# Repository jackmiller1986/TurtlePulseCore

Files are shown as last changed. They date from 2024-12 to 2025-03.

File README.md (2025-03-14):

# BoxTurtle V1.0
BoxTurtle Automated Filament Control (requires AFC-Klipper-Add-On (Beta))

BT_Render
Join me on Discord (https://discord.gg/eT8zc3bvPR)

BoxTurtle is exactly what it appears to be — an open source AMS style filament changer for [Klipper](https://klipper3d.org) machines. 
BoxTurtle requires the AFC-Klipper Add-On (found [here](https://github.com/ArmoredTurtle/AFC-Klipper-Add-On)).
The goal of BoxTurtle is to deliver a user experience as close to an AMS as possible in vanilla Klipper. i.e. an "AMS" for any klipperized printer regardless of form factor but [VORON Design](https://vorondesign.com) printers in particular.

If you appreciate the work we are doing, you can support us [here](https://www.armoredturtle.com/pages/donate).

# How it works

BoxTurtle is a lane based automated filament changing system. Each lane is equipped with its own dedicated extruder that moves filament to and from the tool head independently. Spool management is done with low drag, top fed electric respoolers.

Each lane merges to a hub (combiner) with a sensor with one outlet that goes to the toolhead.

To accommodate any differences in rotation distance between the extruder in the tool head and the lane motors, BoxTurtle uses a toolhead buffer, like [TurtleNeck](https://github.com/ArmoredTurtle/TurtleNeck) by ArmoredTurtle.

For best results we recommend the AFC-Lite, developed by [Isik's Tech @xbst](https://github.com/xbst/AFC-Lite/) as it has the necessary sensor ports and DC brushed motor drivers used for BoxTurtle's electric respoolers.

# For best results

## AFC Klipper Add-On
BoxTurtle was designed in tandem to work with the [AFC Klipper Add-On](https://github.com/ArmoredTurtle/AFC-Klipper-Add-On). For information on installing and configuring the AFC Klipper Add-On, please visit that repository for the most comprehensive detail. Most common configuration options are prompted for during the installation process.  Some of the options presented are covered below at a high level.

The AFC Klipper Add-On requires root access to your SBC running klipper and the ability to install/modify the installation. Additionally, the minimum version for Klipper/Kalico is 0.12.0 and the minimum version for the klippy-env Python installation is 3.x.

## Filament cutter or tip forming?
BoxTurtle works most reliably with a toolhead filament cutter. Our recommended toolhead cutter solution is [FilamATrix](https://github.com/thunderkeys/FilamATrix). Please visit that Github repository for the most up to date instructions and information. Ensure that toolhead cutting is selected during installing the AFC Klipper Add-On, or enable it manually by editing ``AFC/AFC.cfg`` and restarting Klipper.

If a toolhead filament cutter is not a possibility, tip forming is also an option. This is enabled via the installation script or by editing ``AFC/AFC.cfg`` and restarting Klipper. Tip forming is extremely dependent on your printer, filament and even environment and guidance on properly tuning this is outside the scope of this document. Please visit the [ArmoredTurtle Discord](https://discord.gg/eT8zc3bvPR) for community support on tip forming.

## Filament sensor
A pre-extruder toolhead filament sensor is recommended but not required if using a [TurtleNeck](https://github.com/ArmoredTurtle/TurtleNeck) or [TurtleNeck 2](https://github.com/ArmoredTurtle/TurtleNeck2.0) filament buffer. A post-extruder filament sensor can be defined in the AFC configurations, but is not currently used beyond reporting status of the sensor.

Options include:

- [FilamATrix](https://github.com/thunderkeys/FilamATrix)
- [Filatector](https://github.com/ArmoredTurtle/Filatector)
- [AFC Buffer Ram Sensor using TurtleNeck](https://github.com/ArmoredTurtle/AFC-Klipper-Add-On/blob/main/docs/Buffer_Ram_Sensor.md)

## Waste management

### Pooping, Kicking, and Wiping?
One option for filament purge/waste can be to have the printer 'poop' blobs of filament on the bed, have the nozzle cleaned with a brush/wipe, and hten return the toolhead near the blob and kick off the bed using kinematics into a bucket or other waste evacuation system. This works similar to the method used by [Blobifier](https://github.com/Dendrowen/Blobifier), but does not require servo actuation.  Enabling poop/kick/wipe macros can result in more reliable filament changes and color separation, at the cost of additional time during each filament swap. Each option can be enabled or disabled during the AFC installation process, or by editing ``AFC/AFC.cfg`` and restarting Klipper.

### Prime towers
Filament prime towers can be used standalone, or in combination with the above to minimize the chance that no blobs or oozes from the filament change process make it on to your final print. However, if you are using pooping as described above, you likely need far less purging than the default slicer settings suggest. You can adjust the 'flushing volumes' in most slicers, as well as the size of your prime/purge tower. A decent starting setting for these might be a flushing volume multiplier of 0.1-0.2 and a tower width size of 20mm.

If you want to rely solely on the poop purge, a static size wipe tower can be set by disabling the 'Purge into Prime Tower' setting in your slicer software's "Printer Settings".

Different filament color transitions will require different purge volumes, and thus tuning this is highly dependent on your filaments and prints you are performing.

# Enclosure

The enclosure option for BoxTurtle has been moved to its [own repository](https://github.com/ArmoredTurtle/BoxTurtle-Enclosure). The enclosure is still [under development](https://www.youtube.com/watch?v=Jjgi8q28Y2o), but the most up to date information on it can be found at that repository. Also considering [joining the ArmoredTurtle Discord](https://discord.gg/eT8zc3bvPR) to get progress updates as development progresses.

# Errata
Identified known issues and potential workarounds are documented in [ERRATA.md](ERRATA.md).

# Manual

ArmoredTurtle's project manuals are hosted [here](https://armoredturtle.xyz). There is no PDF, this is intended to make the build experience as easy as possible.
[BoxTurtle Assembly Manual](https://armoredturtle.xyz/manual-sections.html?manual=boxturtle)

# Printed Parts

**IMPORTANT NOTE:** This is NOT a [VORON Design](https://vorondesign.com) project, we strongly recommend that you run a profile that is specific to BoxTurtle. Voron parts profiles are not recommended for BoxTurtle printed parts, as the tolerance expetations are different.

Specifically, make sure you are tuning for skew and filament shrinkage. An excellent tool for this is Vector3D's [Califlower Mk2](https://vector3d.shop/products/califlower-calibration-tool-mk2) (yes, it's worth the $14). Do this *before* you print 1.5-2kg worth of filament for BoxTurtle parts!

If you purchased a kit, all of the parts you need to print are located in the [Base_Build](https://github.com/ArmoredTurtle/BoxTurtle/tree/main/STLs/Base_Build) folder under STLs on this repository. There is also a [web-based configurator](https://armoredturtle.xyz/stl-configurator.html) available for easy identification and download of what STLs to print outside of a base kit build.

All parts are pre-oriented for printing and have all required support pre-built into the STLs. OrcaSlicer/BambuStudio (and possible others) may give warnings about certain parts having 'floating cantilevers', these are breakway support structures and these errors can safely be ignored.

If you have an LDO BoxTurtle kit, these are the options to pick on the web-based configurator:

- ``Would you like normal or monolithic skirts?`` - your choice.  If you can fit monolithic on your printer, it has a more unified look vs the split parts. We recommend a 350mm minimum size bed for this, but you may be able to get them to squeak in on a ~300-305mm plate.
- ``Would you prefer a hub or pass through skirts?`` - Hub is our recommended default choice.
- ``Are you using printed corners or extrusion corners?`` - Printed corners
- ``LED corners or plain?`` - Plain
- ``Are you using D2F or D2HW style switches?`` - D2HW
- ``Would you like to print the Hardware or No-Hardware version of the trays?`` - Choose No Hardware if you have a minimum 235x235mm bed.  Some Ender-style printers have a maximum 220x220mm printable voluem, and so the 'bars' that slot into the extrusion require hardware (heatsets/screws) to attach to the tray.
- ``What style tray would you like to print? Plain, Inlay, Multicolor, or Desiccant?`` - Again, a bit of personal choice.  Plain would be the base option, but there's no reason you couldn't print the others.  An enclosure is [in the works](https://www.youtube.com/watch?v=Jjgi8q28Y2o) so if you wanted to future proof for that, desiccant trays are available (in two sizes).
- ``Would you like to print a TurtleNeck buffer?`` - Yes

If all of the above sounds a bit overwhelming, you can print all of the parts in [LDO_BoxTurtle_Kit_STLs.zip]((https://github.com/ArmoredTurtle/BoxTurtle/tree/main/STLs/STLs/LDO_BoxTurtle_Kit_STLs.zip) and they will be the right ones to build a functioning BoxTurtle.

For the 'No Hardware' trays, you may wish to enable 'Thick bridges' or use a 0.25mm first layer height, as otherwise the built in supports may generate 0.4mm gap between the support and the printed part.  The N20 motor mounts may also benefit from an 0.25mm first layer height.

There is a calibration print that you may like to print before getting started [here](https://www.printables.com/model/1004303-box-turtle-calibration-fidget).

# How to create a meshed look on the skirts
There are a few ways to create a 'meshed' look on the hexes on the skirts, using your slicer.

- On the print settings profile, set top and bottom layers to 0.  Adjust infill pattern, density and angle to suit your preference.
- You can also do a height range modifier on the part from 0-3.6mm to set top/bottom layers to 0, and infill pattern, desnity and angle to suit your preference.
- If you would like a different color for the hexes, you can do a color swap at layer 19 (3.8mm with 0.2mm layer heights).
- [SteveBuilds](https://youtube.com/@SteveBuilds) created a custom set of skirt options with modeled in hexes and multibody parts, these can be found [here (multibody)](https://github.com/ArmoredTurtle/BoxTurtle/tree/main/STLs/Option_Parts/Skirts/Multibody/) and [here (modeled hex meshes)]((https://github.com/ArmoredTurtle/BoxTurtle/tree/main/STLs/Option_Parts/Skirts/Hex_Mesh/). To get a two tone color look, perform a color change at 3.2mm (layer 16 at 0.2mm print heights).

# Wiring
BoxTurtle_AFC-Lite_Pinout

Refer to [BT_Wiring/README.md](BT_Wiring/README.md) for recommended wire lengths for each lane.

# PTFE sizes/lengths

**NOTE**: PTFE lengths between extruder to hub are suggested starting lengths - you may need to trim a little bit off in order for it to have a smooth bend. The filament path should be a smooth curve without tight corners.

| Component | Outer Diameter | Inner Diameter | Length | Notes |
|---|---|---|---|---|
| Feeders to Trigger | 4mm | 3mm | 50mm | Quantity 4 ; use PTFE cutter jig |
| Trigger to Extruder | 4mm | 3mm | 80mm | Quantity 4 ; use PTFE cutter jig |
| Extruder to Hub (Outer lanes) | 4mm | 2mm | 171mm | Quantity 2; 3mm ID will blow out. A chamfer is recommended on each end. |
| Extruder to Hub (Inner lanes) | 4mm | 2mm | 101mm | Quantity 2; 3mm ID will blow out. A chamfer is recommended on each end. |
| Hub to Turtleneck | 4mm | 2mm | build dependent | A chamfer is recommended on each end. |
| Turtleneck to toolhead | 4mm | 2-3mm | build dependent | Existing bowden tube is fine, but tighter ID can also be used. |

# Initial startup guide
Please refer to the [Initial Startup Guide](Initial_Startup.md) after completing the assembly of your BoxTurtle for next steps.

# Optional Accesories
Some optional printed accesories for your BoxTurtle build can be found on the [AFC-Accessories](https://github.com/ArmoredTurtle/AFC-Accessories) repository.

# BoxTurtle sourcing/vendors
While BoxTurtle can be mostly self-sourced, some vendors offer partial or full BoxTurtle kits. These vendors also have dedicated channels on the Armored Turtle Discord.

If you purchase a kit from a vendor not on this list, it has not been validated in any way by the ArmoredTurtle team for either quality or completeness. For best results we recommend using a trusted vendor from the list below whenever possible. If you are a vendor and would like to be added to this list, please open a ticket on our Discord to request being added.

US:
- [DLLPDF](https://dllpdf.com) sells a [BoxTurtle frame kit](http://dllpdf.com/box-turtle-frame)
- [Isik's Tech](https://store.isiks.tech/) has BOM parts, including full kits [here](https://store.isiks.tech/collections/box-turtle-parts). Isik's Tech also ships internationally.
- [Fabreeko](https://www.fabreeko.com/products/box-turtle?_pos=4&_psq=box&_ss=e&_v=1.0)
- [KB3D](https://kb-3d.com/store/boxturtle/2132-pre-order-ldo-box-turtle-automated-filament-changer-kit-v10.html)
- [West3D](https://west3d.com/products/box-turtle-automated-filament-changer-multi-material-unit-by-armored-turtle)
  
CA:
- [Sparta3D](https://sparta3d.ca/products/ldo-box-turtle-kit)

EU:
- [Alchemy3D.de](https://alchemy3d.de) has a [BOM in a box kit](https://alchemy3d.de/products/boxturtle)
- [Lab4450.com](https://lab4450.com) resells the [AFC-Lite MCU](https://lab4450.com/product/afc-lite-board/)
- [3DO](https://3do.dk/3d-printer/2946-ldo-boxturtle-afc-kit-til-klipper-printere-forudbestilling.html)

UK:
- [OneTwo3D.co.uk](https://www.onetwo3d.co.uk)
- [Desktop Machine Shop](https://www.desktopmachineshop.com/shop/ldo-boxturtle-afc-kit-v1-0-163?category=4#attribute_values=)
- [Viperworx](https://www.viperworx.uk/product/box-turtle-enclosure-panels-by-armored-turtle)
  
AU:
- [DREMC](https://store.dremc.com.au/products/ldo-box-turtle-hardware-kit)
  
# Merch
- BoxTurtle T-Shirt ($3 from each sale goes to support ArmoredTurtle) via [Cotton Bureau](https://cottonbureau.com/p/QKF5XC/shirt/colored-box-turtle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)- also has sweatshirt/hoodie variants
- BoxTurtle Sticker via [Dr. Mursey](https://drmursey.myshopify.com/products/box-turtle)

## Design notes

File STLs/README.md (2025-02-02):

We have an automatic STL configurator wizard if you need help figuring out what parts to print!

https://armoredturtle.xyz/stl-configurator.html

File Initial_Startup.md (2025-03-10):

# BoxTurtle Initial Startup/Commissioning guide

The following guide will help you on the journey to multicolor printing after you have physically completed the [assembly of your BoxTurtle](https://armoredturtle.xyz).

## Prerequisites

### Calibrate/tune existing printer extruder
If you are installing this on a new printer or extruder (including [FilamATrix](https://github.com/thunderkeys/FilamATrix) ensure you have calibrated your printer/extruder before introducing AFC/multicolor printing. If your extruder rotation distance is off by a large factor, this will cause issues with defining values such as ``tool_stn`` and others later on in the configuration.

It is a lot easier to do some of the calibrations (such as rotation distance) *BEFORE* installing your BoxTurtle.

Our recommended guide to follow for calibration is [Ellis' Print Tuning Guide](https://ellis3dp.com/Print-Tuning-Guide/).

### Ensure minimum system requirements
The AFC Klipper Add-On requires a minimum Klipper/Kalico version of 0.12.0, as well as a correspoding klippy-env python environment at least 3.x.

If you are on Klipper/Kalico 12, but running ``~/klippy-env/bin/python --version`` returns version 2.7.x, you can recreate it with the following.

```
sudo service klipper stop

mv ~/klippy-env ~/klippy-env2.7
virtualenv -p python3 ~/klippy-env
~/klippy-env/bin/pip install -r ~/klipper/scripts/klippy-requirements.txt

sudo service klipper start
```

After recreating it, you may need to reinstall any custom add-ons, such as Klippain Shake&Tune, TMC Autotune, etc.

Ensure you have a clean, functioning klipper install with all of these minimum requirements met before proceeding to the next step.

## Flashing the AFC-Lite board

The AFC-Lite MCU can be connected with either CANBUS or USB.

If you choose to use CANBUS, follow [this guide from Esoterical](https://canbus.esoterical.online/toolhead_flashing/common_hardware/AFC-Lite/README.html).  This site also has a wealth of information on how to configure CANBUS if this is your first time using it.

If you choose to use USB, you will still need to run a 24 V+/V- cable to the AFC-Lite canbus port, just leave the CAN High/Low pins unpopulated. To flash the AFC-Lite for use with USB for data, follow [this guide from Esoterial](https://usb.esoterical.online/hardware_config/STM32/AFC_Lite.html)

Further details regarding the AFC-Lite can be found [in the AFC-Lite manual](https://github.com/xbst/AFC-Lite/blob/master/Docs/AFC-Lite_Manual.pdf).

After flashing and setting up connections/configurations appropriately, you should be able to either obtain the CANBUS UUID (if using CAN) or the device serial path (e.g., ``/dev/serial/by-id/...``) (if using USB) for the AFC-Lite MCU.  Please ensure you have these values before you proceed, as they will be required.

## Make note of any toolhead sensor pins
If you are using [FilamATrix](https://github.com/thunderkeys/FilamATrix), and are using toolhead endstop sensors, make a note of what MCU pins those sensors are connected for the pre-extruder gear sensor (aka ``pin_tool_start``) and post-extruder gear sensor (``pin_tool_end``). Use these in the next step to properly install and configure AFC.

If you do not have a native toolhead filament sensor, you can use either an inline filament sensor such as [Filatector](https://github.com/ArmoredTurtle/Filatector), or you can use the [TurtleNeck buffer](https://github.com/ArmoredTurtle/TurtleNeck) as a virtual toolhead endstop, please see [this guide](https://github.com/ArmoredTurtle/AFC-Klipper-Add-On/blob/main/docs/Buffer_Ram_Sensor.md) for more details.

## Install the AFC Klipper Add-On
BoxTurtle works best with the [AFC Klipper Add-On](https://github.com/ArmoredTurtle/AFC-Klipper-Add-On).  The rest of this guide will focus on configuring AFC for use with BoxTurtle.

Follow the instructions on that Github for latest details on installation and configuration, but at the time of writing this is the easy button:

```
cd ~
git clone https://github.com/ArmoredTurtle/AFC-Klipper-Add-On.git
cd AFC-Klipper-Add-On
./install-afc.sh
```

The default options for the park, cut, kick, wipe, and tip forming macros can be used if you don't know what to choose. These can all be changed later by editing ``AFC/AFC.cfg`` and doing a firmware restart.

After installation, please ensure sure you update the following settings:
- In ``AFC/AFC_Turtle_1.cfg``:
  - ``canbus_uuid`` if using CANBUS
  - ``serial`` if using USB
- In ``AFC/AFC_Hardware.cfg``
  - ``pin_tool_start`` and/or ``pin_tool_end``

In your ``printer.cfg``'s ``[extruder]`` section, update the setting ``max_extrude_only_distance`` to the value 400.  If the setting is not there, add it:

```max_extrude_only_distance: 400```

For best results, reboot your printer after installing the Add-On and including it in your printer.cfg.  This will ensure all required modules are enabled.

## First self-test
AFC will run a self-test automatically on startup. It will run through the respoolers on each lane (from left to right, lanes 1-4) and will update the lightbox LED indicating status for each lane.

The default status indicators are:

- Red: No filament loaded/detected at extruder sensor
- Green: Filament loaded to lane extruder sensor
- Blue: Filament loaded to toolhead
- White: Filament in process of being loaded

After the self-test completes, you hopefully will see a picture of a happy turtle in the console log! If you get a picture of an error turtle, you may have a misconfigured AFC setting, broken pin or some other issue that needs attention.

You can display the status of sensors in Mainsail/Fluidd as regular filament switches by setting ``enable_sensors_in_gui: True`` either globally in ``AFC/AFC.cfg`` or in the individual component section (e.g. extruders in ``AFC/Turtle_1.cfg``.

If you are unable to resolve the error after visiting the [troubleshooting guide](https://github.com/thunderkeys/AFC-Klipper-Add-On/tree/main?tab=readme-ov-file#troubleshooting), you can get support from the community on the Armored Turtle discord by opening a help thread (run the Discord command ``/help``) to learn how).

## Further tests

### Respoolers
Run the ``TEST`` command against each lane (one at a time) to verify proper respooler operation:
- ``TEST LANE=lane1``
- ``TEST LANE=lane2``
- ``TEST LANE=lane3``
- ``TEST LANE=lane4``

Verify that each respooler works properly before proceeding.

### Trigger switches
Actuating the trigger switch should begin pulsing that lane's extruder motor to load filament.  Verify that the switch being actuated is activating that same lane's extruder motor.

Once all four lanes are confirmed to be activating the correct extruder when the trigger switch is actuated, move on to the next step.

### Extruders
Insert filament into the feeder tube (it helps to cut it at an angle) and press through until the extruder motor gears catch the filament and load it further.  If you can press the filament through but it feels like the extruder motor is pushing back on the filament instead of pulling it in, try reversing the ``dir_pin`` setting for that extruder motor in ``AFC/AFC_Turtle_1.cfg``.

If you are able to load filament into all 4 lanes and get a green LED indicator, and ``AFC_STATUS`` at the console reports no errors, move on to the next step.

### TurtleNeck buffer
Test that TurtleNeck buffer is configured correctly by extending the slide all the way out, then run ``QUERY_BUFFER BUFFER=Turtle_1``.  This should return ``Trailing``.  Collapse the slide all the way so it triggers the switch at the rear, then rerun the QUERY_BUFFER command.  It should then report ``Advancing``.

Confirm proper operation of your TurtleNeck before proceeding.

## Setting up hotend specific values
Some of the values with AFC are extremely dependent on your hotend.

Suggested starting values for hotend types (more to be added later).  ``tool_stn`` and ``tool_stn_unload`` are in ``AFC/AFC_Hardware.cfg``, ``variable_retract_length`` and ``variable_pushback_length`` are in ``AFC/AFC_Macro_Vars.cfg``.  For ``tool_stn``, if you have ``pin_tool_end`` defined, use the second value; otherwise, use the first value. You may need to increase this value if you are using a ram buffer as the toolhead sensor.

| Hotend | tool_stn | tool_stn_unload | variable_retract_length | variable_pushback_length
| ------ | -------- | --------------- | ----------------------- | ------------------------
| Revo Voron | 52 (if ``pin_tool_end`` is NOT defined) / 29 (if ``pin_tool_end`` is defined) | 62 | 22 | 20 |
| Rapido HF | 64.1 (if ``pin_tool_end`` is NOT defined) / 41.1 (if ``pin_tool_end`` is defined) | 105.9 | 10 | 10 |
| Rapido V2 HF | 74 (if ``pin_tool_end`` is NOT defined) / 52 (if ``pin_tool_end`` is defined) | 81 | 25 | 20 |

## Setting up macro variables

### A note on order of operations of macros during tool changes
AFC will perform macros (if enabled) on each tool change (``T0``, ``T1``, etc) in the following order:

- Load sequence
  - If toolhead is loaded from another lane, that will first be unloaded (see below sequence)   
  - Poop
  - Wipe/Brush
  - Kick
  - Wipe/Brush
  - Print 
- Unload sequence
  - If toolhead cutter is enabled:
     - Cut
     - Park
  - If tip forming is enabled:
     - Park
     - Tip Form

### Uncommon variables
AFC has many variables that you can tweak for macros, including definition of complete custom macros to replace the stock ones. Most users will never need to touch these and they will not be covered in this guide. Below are the most common variables that will need adjusting for a stock BoxTurtle configuration with a Stealthburner/FilamATrix toolhead.

For more details, please refer to the AFC-Klipper-Add-On Github docs or the comments in the ``AFC/AFC.cfg`` and ``AFC/AFC_Macro_Vars.cfg`` files.

If you chosen not to enable a macro during the installation, the command will still show in mainsail, and have a configuration in AFC_Macro_Vars.cfg, but it will not be called during the load/unload sequences.

#### Park
The park macro is enabled or disabled by setting the ``park`` variable in ``AFC/AFC.cfg`` (this is prompted for during the install script, but you can change it at any time and do a firmware restart to enact the change.)

Adjust the following macro variables in ``AFC/AFC_Macro_Vars.cfg`` for the park macro (if enabled) for your specific printer.
  - ``variable_park_loc_xy`` - This is the X,Y coordinate your toolhead will park at prior to other filament changes.

#### Cut
The cut macro is enabled or disabled by setting the ``tool_cut`` variable in ``AFC/AFC.cfg`` (this is prompted for during the install script, but you can change it at any time and do a firmware restart to enact the change.)
Adjust the following macro variables in ``AFC/AFC_Macro_Vars.cfg`` for the cut macro (if enabled) for your specific printer. 
  - ``variable_retract_length`` - How much to retract filament before performing the cut. This reduces purge waste and improves reliability of insertion of the next filament. Hotend dependent, a good starting value is the length of your meltzone. Please see the hotend diagrams for suggested values. The default is ``20``.
  - ``variable_pin_loc_xy`` - X,Y position where your toolhead cutter arm *just* touches the depressor pin.  There is no default value, this must be defined.
  - ``variable_cut_direction`` - For FilamATrix, you want this to be set to ``left``. Other toolhead cutters may actuate in a different direction (e.g., Dragon Burner cutter may be ``front``).  The default value is ``left``.
  - ``variable_pin_park_dist`` - How far to park the toolhead near the depressor pin before initiating the move. This acts as a safety as well as helps generate momentum for the cut. The default value is ``6.0``.
  - ``variable_cut_move_dist`` - How far the toolhead has to move from ``variable_pin_loc_xy`` to fully depress the cutter. This should be reduced from the actual value by 0.5mm as a buffer to prevent skipped steps. The default value is ``8.5``
  - ``variable_cut_count`` - How many times to attempt the cut. The default value is ``2``, to ensure a clean/complete cut.

#### Poop
The poop macro is enabled or disabled by setting the ``poop`` variable in ``AFC/AFC.cfg`` (this is prompted for during the install script, but you can change it at any time and do a firmware restart to enact the change.)

Adjust the following macro variables in ``AFC/AFC_Macro_Vars.cfg`` for the poop macro (if enabled) for your specific printer.
  - ``variable_purge_loc_xy`` - X,Y position where to perform the poop operation. Usuually, this is on the corner of your bed.

#### Kick
The kick macro is enabled or disabled by setting the ``kick`` variable in ``AFC/AFC.cfg`` (this is prompted for during the install script, but you can change it at any time and do a firmware restart to enact the change.)
Adjust the following macro variables in ``AFC/AFC_Macro_Vars.cfg`` for the kick macro (if enabled) for your specific printer.
  - ``variable_kick_start_loc`` - the X, Y, Z location to move to prior to begin the kick operation. If you do not want a Z move, set the Z coordinate to ``-1``.
  - ``variable_kick_direction`` - the direction to move to kick the poop off (left, right, front, back)
  - ``variable_kick_move_dist`` - how for to move in that direction to kick the poop off

#### Wipe/Brush
The wipe macro is enabled or disabled by setting the ``wipe`` variable in ``AFC/AFC.cfg`` (this is prompted for during the install script, but you can change it at any time and do a firmware restart to enact the change.)
Adjust the following macro variables in ``AFC/AFC_Macro_Vars.cfg`` for the brush macro (if enabled) for your specific printer.
  - ``variable_brush_loc`` - X, Y, Z coordinates of the center of the brush. If you do not want a Z move, set the Z coordinate to to ``-1``.
  - ``variable_y_brush`` - Set to ``true`` if you want the macro to do a brush in the Y direction first before doing X. When set to ``false``, only it will move only in the X direction.
  - ``variable_brush_width`` and ``variable_brush_depth`` - the width and depth of your brush, in mm.
  - ``variable_brush_count`` - Number of passes to make on the brush, the default is ``4``.

#### Tip forming
**NOTE**: While a toolhead cutter is recommended for best results, if you do not have one you will need to configure tip forming. The full process for this is outside the scope of this document and will be very hotend and perhaps even filament dependent. If using a 'Hub Cutter' (e.g., BT-Snappy or EREC) you will still likely need to do tip forming to prevent stringy tips from getting jammed in the toolhead, hub or BoxTurtle extruder gears.

Tip forming is enabled or disabled by setting the ``form_tip`` variable in ``AFC/AFC.cfg`` (this is prompted for during the install script, but you can change it at any time and do a firmware restart to enact the change.)

Adjust the following tip forming variables in ``AFC/AFC.cfg`` for tip forming (if enabled) for your specific printer. Note the different location that the above macros.
  - ``cooling_tube_position`` - Starting location of the cooling tube in mm (based off toolhead sensor)
  - ``cooling_tube_length`` - Length of the cooling move in mm
  - ``cooling_moves`` - number of cooling moves to perform, the default is ``4``.

### Enacting changes
Perform a ``FIRMWARE_RESTART`` (a full printer reboot is not required) after adjusting all the macro variables in ``AFC/AFC_Macro_Vars.cfg`` file.

## Calibration
Follow [this guide](https://github.com/thunderkeys/AFC-Klipper-Add-On/blob/main/docs/Calibration.md) to calibrate the necessary lengths of your BoxTurtle.

Note that these values may need to be tweaked slightly if the loading sequence does not function.  Make small adjustments (5/10mm) to see if performance/reliability improves.

## First load of filament to toolhead

You're now ready to attempt your first Automated Filament Control action!

- Home your printer (using G28 or Mainsail/Fluidd GUI buttons)
- Heat the hotend to your filament's extrusion temperature (e.g., PLA 210, ABS 260, etc).
- Load the filament for lane 1 with with the ``T0`` command.
- Confirm that filament travels to the toolhead and performs any configured poop or wipe actions.  After the load has successfully completed, test that you are able to manually extrude filament using the console/GUI.
- Change filament to lane 2 using the ``T1`` command.  Confirm that the toolhead moves to the park position, performs the cut (or tip shaping, if not using a cutter), retracts the filament for lane 1 back to the BoxTurtle hub.  It will then load the filament in lane 2 to the toolhead, and perform the poop, wipe, kick and wipe macros.
- Repeat this process for lane 3 (``T2``) and lane 4 (``T3``).

If you are able to successfully load and unload filament without intervention, you are ready to move on to the next step. Almost there!

### Configuring your slicer

The recommended slicer for AFC is OrcaSlicer. Other slicers such as PrusaSlicer or SuperSlicer may be used, and the configuration of options within them is similar but naming or options may be slightly different.

#### Updating printer settings in Orca
For the printer you are adding BoxTurtle to, first go to the Printer settings, Multimaterial tab and ensure settings are configured as per the below screenshot.
![Orca_Printer_Settings](https://github.com/user-attachments/assets/1aa56051-dbbf-49a4-b818-368e00406b17)

Also, on the Extruder 1 setting page - reduce ``Retraction while switching material`` length from the default of 2 to 0.5. (PrusaSlicer/SuperSlicer users, this default is 10mm and is on each extruder under the printer settings).

#### Adding additional filaments/extruders
Increase the number of filaments to match your BoxTurtle's lane count. 
![Orca_Add_Filament_Settings](https://github.com/user-attachments/assets/61fb26a4-57c6-4624-8435-478d719a01ae)

#### Updating the Machine G-code settings

- Set ``Machine start G-code` appropriately for your printer, specifically adding the ``TOOL={initial_tool}`` to your ``PRINT_START`` macro.
```
M104 S0 ; Stops OrcaSlicer from sending temperature waits separately
M140 S0 ; Stops OrcaSlicer from sending temperature waits separately
PRINT_START EXTRUDER=[nozzle_temperature_initial_layer] BED=[bed_temperature_initial_layer_single] TOOL={initial_tool}
```

- Set ``Change Filament G-Code`` to the below value.  Remove any other custom code here, e.g. extruder moves.
```
T[next_extruder]
```

#### Additional Slicer configuration - pre-OrcaSlicer 2.2.0
Configuring per-material filament ramming is no longer required as of the official OrcaSlicer 2.2.0 release (PR [#6934](https://github.com/SoftFever/OrcaSlicer/pull/6934)).  If you are on an earlier version than that (including betas/release candidates) you will need to make the following additional changes to your slicer configurations.
#### Material Settings
![Orca_Material_Settings](https://github.com/user-attachments/assets/a1569e5a-24c5-48f9-98fb-26465bf7c75c)
##### Ramming Settings
Because the AFC-Klipper-Add-On handles any tip forming in the extension, we need to disable these specific settings in the slicer software.  Below is a screenshot for OrcaSlicer, but most Slic3r-based slicers have a similar dialog/setting.
![Orca_Ramming_Settings](https://github.com/user-attachments/assets/2744fb86-afae-4645-9215-3f8507558509)

## Updating your PRINT_START macro
#### *Please note this is just an example macro to show how to incorporate the initial tool into your print start macro. Please adjust it to match your printer setup. A good starting point for a PRINT_START macro is [jontek2's "A Better PRINT_START macro"](https://github.com/jontek2/A-better-print_start-macro)*

Add the TOOL parameter we added to the Machine start G-Code earlier to your PRINT_START macro.

```
[gcode_macro PRINT_START]
gcode:
  {% set BED_TEMP = params.BED|default(60)|float %}
  {% set EXTRUDER_TEMP = params.EXTRUDER|default(195)|float %}
  {% set S_EXTRUDER_TEMP = 150|float %}
  {% set initial_tool = params.TOOL|default("0")|int %}

  G90 ; use absolute coordinates
  M83 ; extruder relative mode

  G28 # Home Printer
  # Do any other leveling such as QGL here

  AFC_PARK

  M140 S{BED_TEMP} # Set bed temp
  M109 S{EXTRUDER_TEMP} # wait for extruder temp
  T{initial_tool} #Load Initial Tool

  M104 S{S_EXTRUDER_TEMP} # set standby extruder temp
  M190 S{BED_TEMP} # wait for bed temp

  G28 Z

  # Bedmesh or load bedmesh

  AFC_PARK
  M109 S{EXTRUDER_TEMP} ; wait for extruder temp

  # Add any pre print prime/purge line here
  # Start Print
```

If you are modifying an existing macro:
- Add the following to the top of the PRINT_START macro just under the ``gcode:`` line
```
  {% set BED_TEMP = params.BED|default(60)|float %}
  {% set EXTRUDER_TEMP = params.EXTRUDER|default(195)|float %}
  {% set S_EXTRUDER_TEMP = 150|float %}
  {% set initial_tool = params.TOOL|default("0")|int %}
```
- Home the printer using ``G28``
- Set hotend to extrusion temperature ``M104 S{EXTRUDER_TEMP}``
- Load the first filament to be used with ``T{initial_tool}``
- Move to park position with ``AFC_PARK``
- Lower the hotend to standby temperature with ``M104 S{S_EXTRUDER_TEMP}``
- Perform any other necessary pre-flight tasks (e.g., heat soak, re-homing Z, bed meshing, prime/purge line, etc)

## Troubleshooting
If you get a klipper error about GSTAT Resets as in the example below:

```
TMC 'AFC_stepper lane1' reports error: GSTAT:      00000001 reset=1(Reset)
```

This may be due to static building up in the system from the PTFE tubing in dry/low humidity environments. Many users have found that running a ground wire from the stepper motor screws to a commond GND pin on the AFC-Lite board, resolves this issue. One example way to do this is below:

For each motor:
- Replace the M3x8 extruder motor mount screw with an M3x12 screw.
- Crimp a ring connector on a wire. Place an m3 washer over the now extended motor mount screw, followed by the ring terminal, followed by an M3 hex or nyloc nut.

Join the wires from all the motors into a 5 port [WAGO 221-415](https://www.wago.com/us/wire-splicing-connectors/compact-splicing-connector/p/221-415). In the 5th port, run a wire from the WAGO to any spare ground pin on the AFC-Lite board (e.g., the GND pin on RGB2).

## Time for cereal!
If you have completed all of the above, you are ready to attempt a BoxTurtle serial (cereal) print.  The latest information on the serial print can be found on the Armored Turtle discord in the [\#serial-info](https://discord.com/channels/1229586267671629945/1282095413046022214) channel.

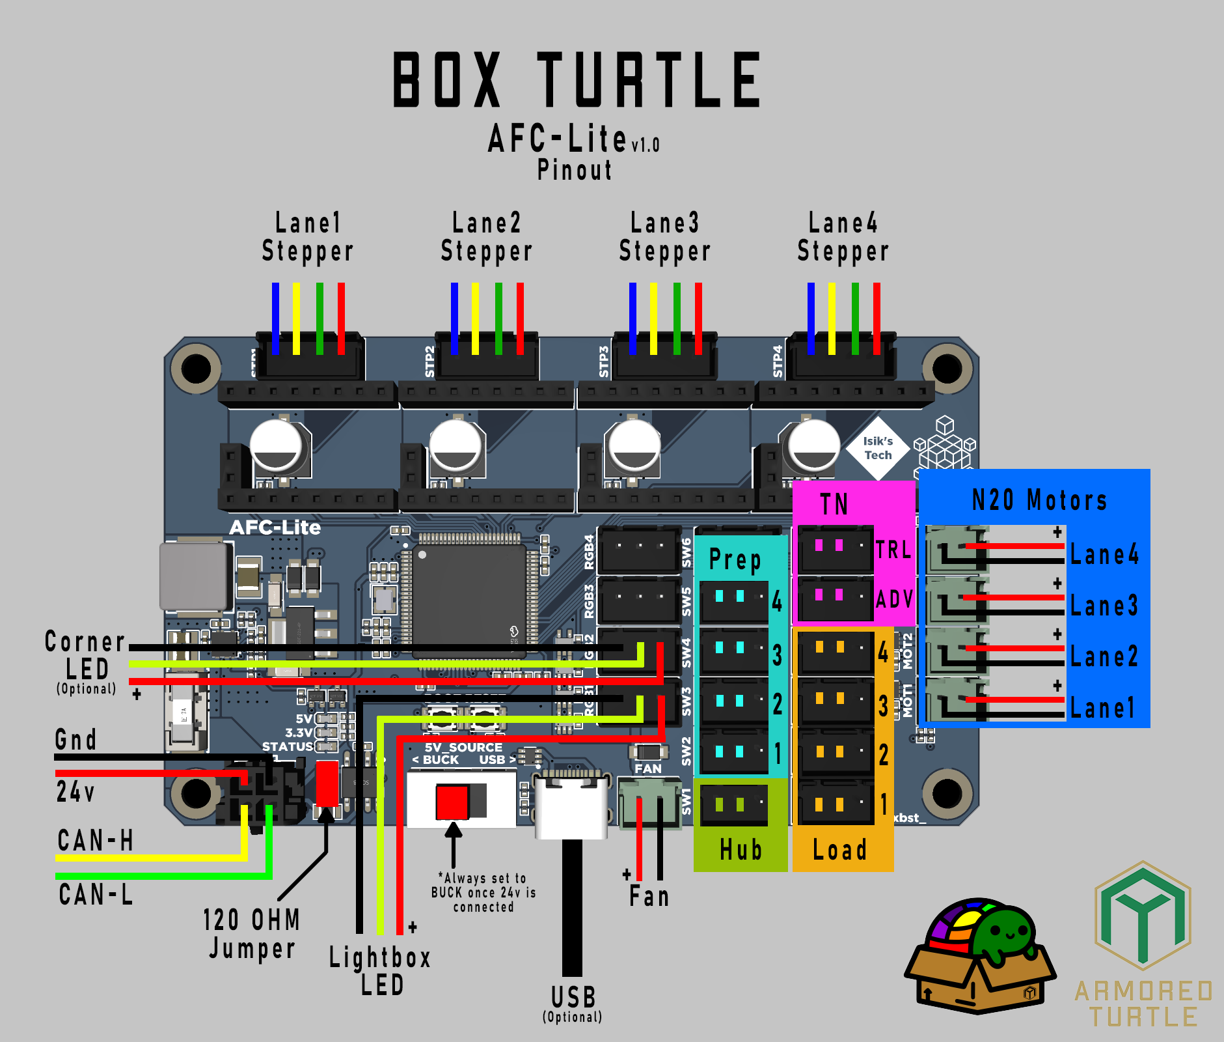
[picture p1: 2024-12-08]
BT_Wiring/BoxTurtle_AFC-Lite_Pinout.png

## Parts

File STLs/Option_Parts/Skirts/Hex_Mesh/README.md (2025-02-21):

Monolith skirts with modeled in Hexagon meshes, courtesy of [Steve Builds](https://github.com/stvptrsn/Printer_Stuff/tree/main/BoxTurtle/Skirts).

Front and rear skirts require a minimum 300mm x 300mm bed to print. If you bed is smaller you can use the cut tool in your slicer to split them to size, or use the pre-cut STLs in this repository.

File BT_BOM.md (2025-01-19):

# BoxTurtle Bill of Materials (BOM)

## Frame

| Item | Quantity | Notes | Links |
| -----|---|---|---|
360mm 2020 Extrusion | 4 | HFSB5-2020-360-TPW |
220mm 2020 Extrusion | 4 | HFSB5-2020-220-TPW |

## Electronics
| Item | Quantity | Notes | Links |
|---|---|---|---|
NEMA14 10 Tooth pancake stepper | 4 |  | [AliExpress](https://www.aliexpress.us/item/3256804884302626.html) <br/> [IsiksTech](https://store.isiks.tech/products/pancake-stepper)
AFC-Lite Board | 1 | | [IsiksTech](https://store.isiks.tech/products/afc-lite)
TMC2209/2226 Drivers | 4 | | [IsiksTech](https://store.isiks.tech/products/tmc2209-step-sticks)
RGBW LED PCB (WS2812) | 4 | | [AliExpress](https://www.aliexpress.us/item/3256801785673787.html)
N20 6v / 500RPM motors | 4 | | [AliExpress](https://www.aliexpress.us/item/2251832836005412.html) <br/> [AliExpress](https://www.aliexpress.us/item/3256805684127036.html) <br/> [IsiksTech](https://store.isiks.tech/products/bt-n20-motors)
D2F-L (with Lever) | 4 | |
D2HW-C201H | 5 | | 
3010 Axial Fan 5v | 1 | Optional | https://www.aliexpress.us/item/3256802884825067.html

## Bearings
| Item | Quantity | Notes | Links |
|---|---|---|---|
| MR63ZZ bearing | 13 | | [AliExpress](https://www.aliexpress.us/item/3256801934742685.html)
| MR148ZZ bearing | 16 | | [AliExpress](https://www.aliexpress.us/item/2251832648440163.html)

## Fasteners (also available as a kit from [Isik's Tech](https://store.isiks.tech/products/box-turtle-stainless-fastener-kit))
| Item | Quantity | Notes | Links |
|---|---|---|---|
| M2x10 Self-tapping screw | 8 | |
| M3x16 BHCS | 4 | Only if using fan |
| M3x30 BHCS | 4 | |
| M3x6 SHCS | 24 | |
| M3x8 SHCS | 78 | |
| M3x10 SHCS | 16 | |
| M3 threaded heatset insert | 70 | |
| M3 washer | 8 |  |
| M5x16 BHCS | 20 | |
| M5 washer | 4 | |
| M5 hex nut | 4 | |

## Miscellaneous Hardware
| Item | Quantity | Notes | Links |
|---|---|---|---|
| 8mm diameter / 80 mm long shaft | 4 | | [AliExpress](https://www.aliexpress.us/item/2255800287548941.html)
| BMG Gear kit | 4 | | [AliExpress](https://www.aliexpress.us/item/3256805442986544.html)
| 6mm x 3mm magnet | 8 | N35 These do not need to be strong | [IsiksTech](https://store.isiks.tech/products/n52-6mm-diameter-3mm-thick-neodymium-magnet)
| ECAS04 Bowden coupler | 17-20 | 17 for hub, 20 for passthrough | [AliExpress](https://www.aliexpress.us/item/3256806432021232.html)
| PG7 Cable Strain relief | 1 | Optional |
| M3 roll-in nuts | 2 | |
| 4mm OD / 3mm ID Bowden tube | ~0.6m |  |
| 4mm OD / 2mm ID Bowden tube | ~3m |  |
| JST-SM 3-pin connectors and crimps | 5 male, 5 female | For creating quick disconnect LED strings per the wiring guide | [AliExpress](https://www.aliexpress.us/item/3256802954473489.html) - 200pc box JST-SM variant

## TN Buffer BOM
| Item | Quantity | Notes | Links |
|---|---|---|---|
| D2F-L (With Lever) | 2 | |
| M2x10 Self-tapping screw | 4 | |
| M3x8 SHCS | 4 | |
| M3 threaded heatset insert | 4 | |
| ECAS04 bowden coupler | 2 | |

## BoxTurtle Hard Mount Legs BOM
| Item | Quantity | Notes | Links |
|---|---|---|---|
| M3 roll-in nuts | 12 | |
| M3x10 SHCS | 12 | |

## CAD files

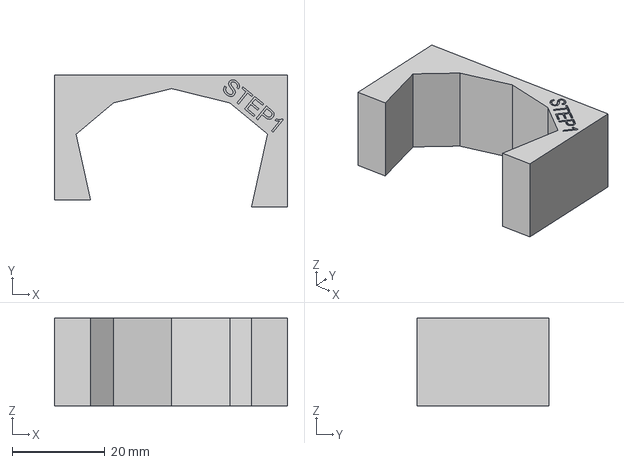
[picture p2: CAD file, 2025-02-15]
CAD/hub_tool_step1.step
50.4 x 28.6 x 19.0 mm

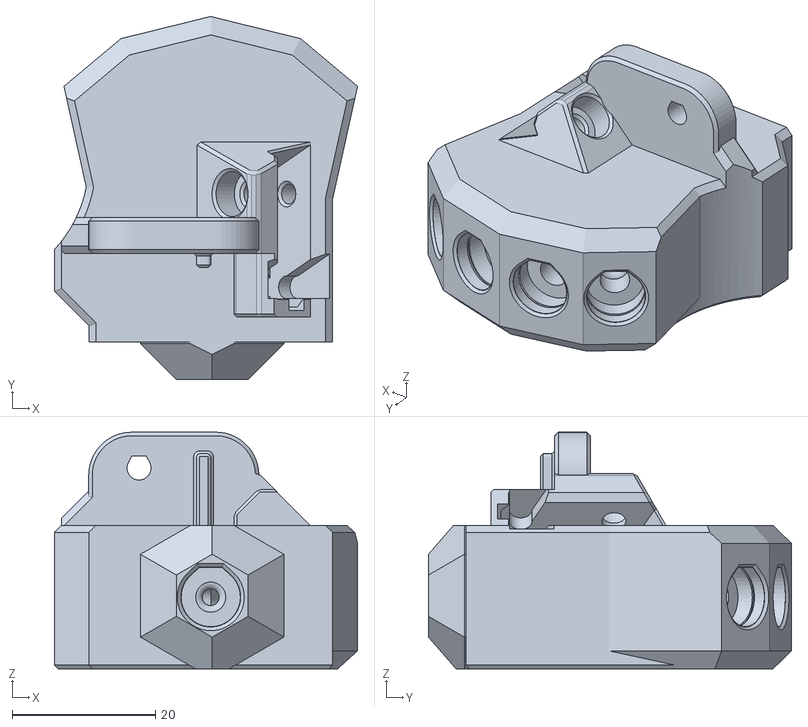
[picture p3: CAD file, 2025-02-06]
STLs/Base_Build/[a]_hub.stl
42.3 x 50.6 x 33.0

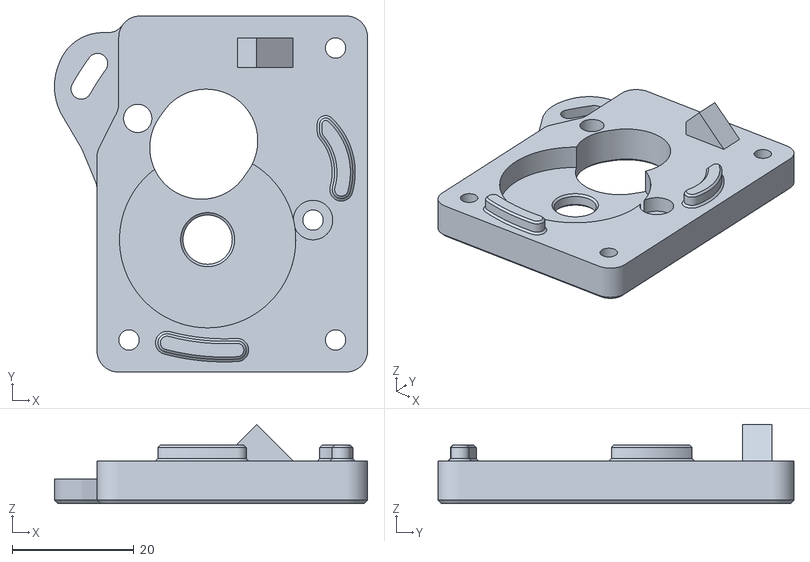
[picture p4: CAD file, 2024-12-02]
STLs/Base_Build/Extruder/motor_plate_x4.stl
51.5 x 58.6 x 13.1

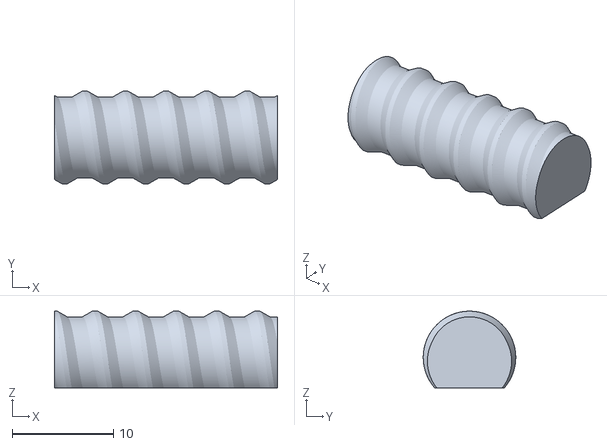
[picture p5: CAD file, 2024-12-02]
STLs/Base_Build/Idlers/idler_threaded_joint_x4.stl
22.0 x 9.13 x 7.57

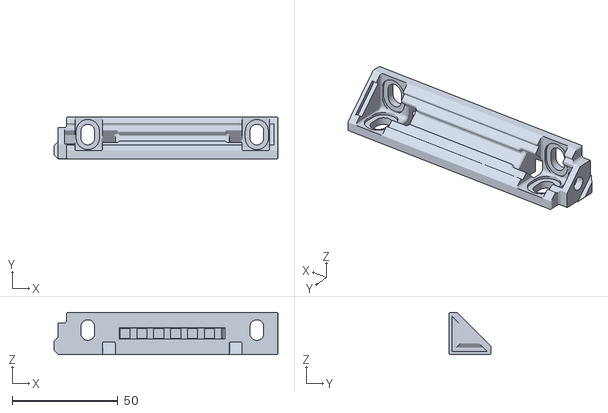
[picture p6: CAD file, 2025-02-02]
STLs/Base_Build/Printed_Corners/corner_printed_x4.stl
106.0 x 20.0 x 20.0

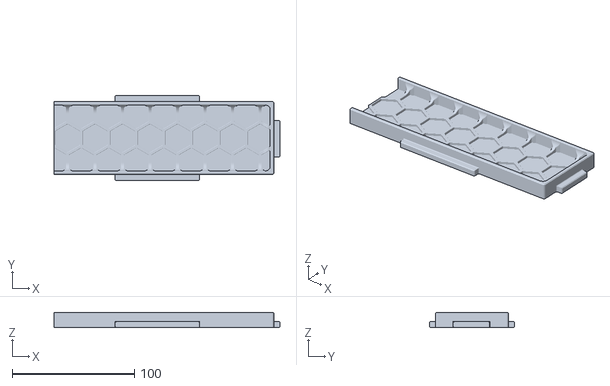
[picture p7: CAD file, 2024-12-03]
STLs/Base_Build/Skirts/skirt_front_hex_R.stl
184.8 x 69.6 x 12.5

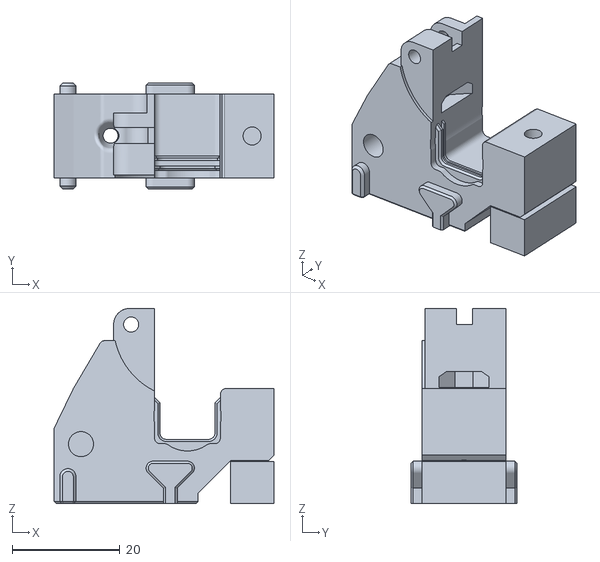
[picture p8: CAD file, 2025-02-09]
STLs/Base_Build/Spooler/motor_mount_x4.stl
40.8 x 19.7 x 36.3

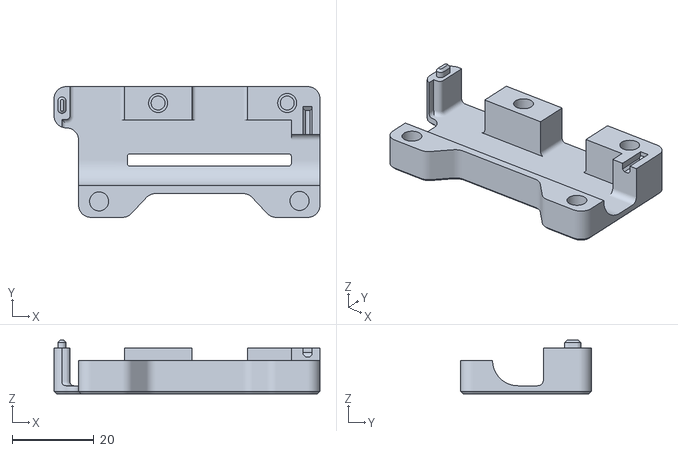
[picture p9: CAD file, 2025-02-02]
STLs/Base_Build/TurtleNeck/lid.stl
64.9 x 31.9 x 13.1

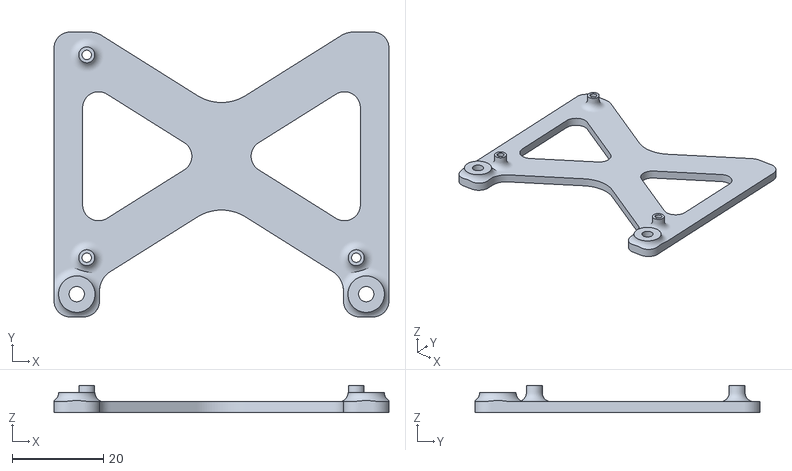
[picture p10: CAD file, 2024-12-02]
STLs/Option_Parts/electronics/mosfetti_mount.stl
73.5 x 62.5 x 6.00

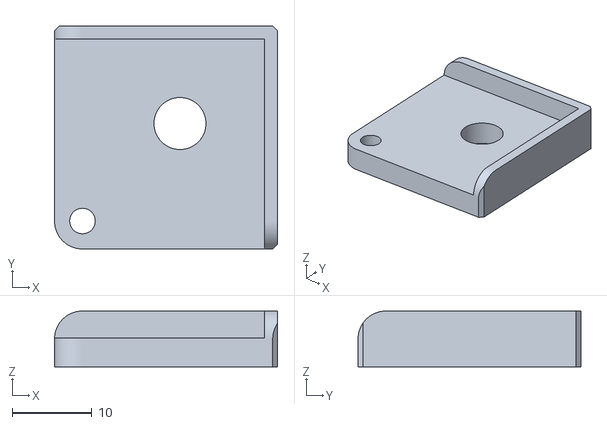
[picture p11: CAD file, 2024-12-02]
STLs/Option_Parts/Extrusion_Corners/[a]_foot_extrusion_x4.stl
27.9 x 27.9 x 7.00

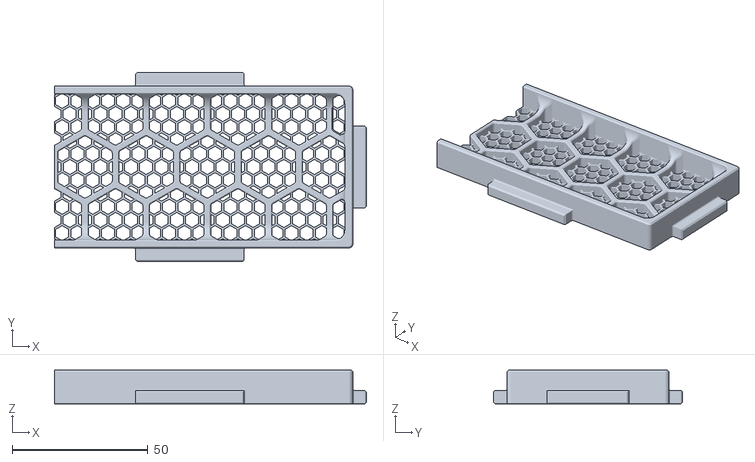
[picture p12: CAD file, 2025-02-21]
STLs/Option_Parts/Skirts/Hex_Mesh/Hex_Side_Part2_Mesh_x2.stl
114.8 x 69.6 x 12.5

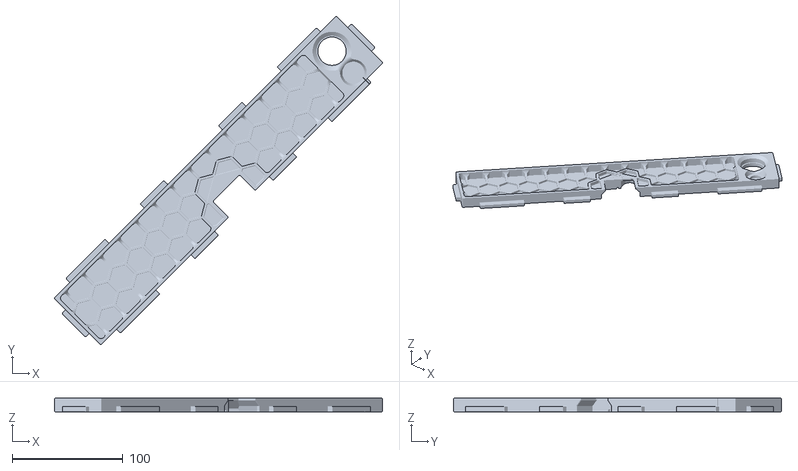
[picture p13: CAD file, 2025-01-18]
STLs/Option_Parts/Skirts/mono_skirt_hub.stl
295.7 x 295.7 x 12.4

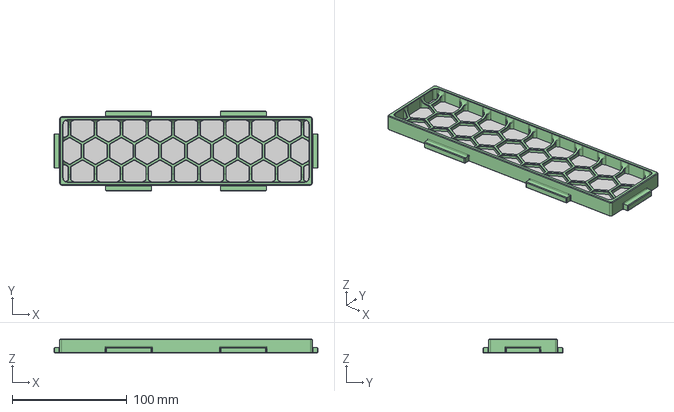
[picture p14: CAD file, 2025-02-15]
STLs/Option_Parts/Skirts/Multibody/Hex_Side_1pc_Solid.step
229.6 x 69.6 x 12.5 mm
Hex_Side
Inserts

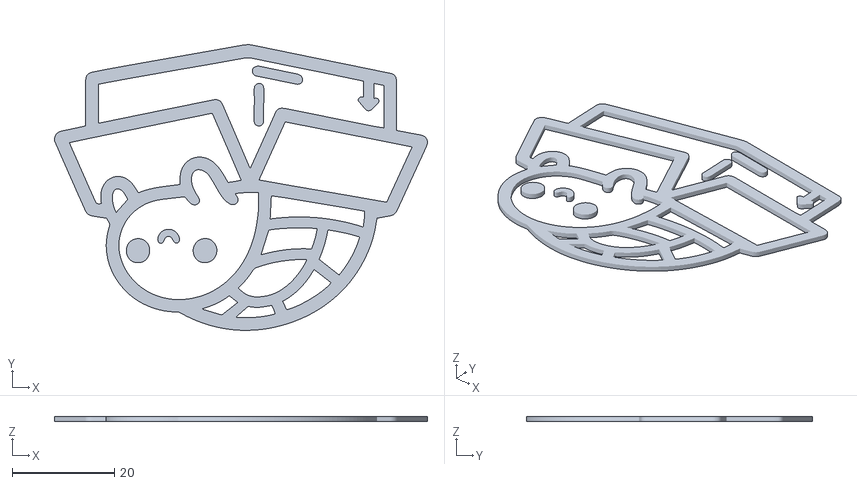
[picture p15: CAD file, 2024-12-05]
STLs/Option_Parts/trays/[a]_logo_inlay.stl
73.0 x 55.9 x 1.00

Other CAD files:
STLs/Base_Build/Tools/hub_tool_step1.stl
STLs/Option_Parts/trays/no_hw/tray_multicolor.3mf
STLs/Option_Parts/trays/w_hw/hw_tray_desiccant.stl
STLs/Option_Parts/trigger_depressor_x4.stl
CAD/BT_Voron_hard_mount.step
CAD/Skirt_Alternatives/Hex_Front_1pc.f3d
CAD/Skirt_Alternatives/Hex_Rear_1pc.f3d
CAD/Skirt_Alternatives/Hex_Side_1pc.f3d
CAD/hub_tool_step2.step
CAD/motor_mount_helper.step
STLs/Base_Build/Extruder/[a]_guidler_x4.stl
STLs/Base_Build/Extruder/extruder_housing_x4.stl
STLs/Base_Build/Idlers/[a]_idler_roller_x8.stl
STLs/Base_Build/Printed_Corners/[a]_foot_x4.stl
STLs/Base_Build/Printed_Corners/[c]_corner_diffuser_x4.stl
STLs/Base_Build/Printed_Corners/foot_tpu_x4.stl
STLs/Base_Build/Printed_Corners/led_corner_cover_x4.stl
STLs/Base_Build/Printed_Corners/led_frame_x4.stl
STLs/Base_Build/Printed_Corners/panel_spacer_x4.stl
STLs/Base_Build/Printed_Corners/solid_corner_cover_x4.stl
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

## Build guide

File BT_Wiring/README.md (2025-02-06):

# BoxTurtle Wiring Guide

## Lane numbering

Lane 1 = leftmost filament lane\
Lane 4  = rightmost filament lane

## AFC-Lite Wiring guide

Prep = Trigger Filament Sensor Switches\
Load = Extruder Filament Sensor Switches

BoxTurtle_AFC-Lite_Pinout

**NOTE**: You need to connect 24V and GND to the CANBUS port pins even if you are connecting using USB-C for data transmission. The AFC-Lite PCB does not support USB Power Delivery.

## Extruder Steppers
| Lane | Recommended Wire Length | Recommended Wire Gauge | Connector |
| ---- | --- | --- | ---|
| Lane 1 | 210mm | Dependent on motor | JST-XH-4 |
| Lane 2 | 320mm | Dependent on motor | JST-XH-4 |
| Lane 3 | 420mm | Dependent on motor | JST-XH-4 |
| Lane 4 | 520mm | Dependent on motor | JST-XH-4 |

##  Indicator LEDs
The default configuration of the LED indicators is to create a neopixel chain of 4 LEDs, using DOUT on one LED to go to DIN of the next LED. JST-SM connectors are spec'd to provide easy disconnect for lane service, but any wire-to-wire connector can be used in their place (e.g. Molex Microfit 3).

| Lane | Component | Recommended Wire Length | Recommended Wire Gauge | Connector |
| ---- | --- | --- | ---| --- |
| Lane 1 | [WS2812 PCB](WS2812_PCB.png) | 130mm/130mm tail | 26-30ga | [JST-SM-M](JST-XH_JST-SM.png)/JST-SM-F |
| Lane 2 | [WS2812 PCB](WS2812_PCB.png) | 130mm/130mm tail | 26-30ga | [JST-SM-M](JST-XH_JST-SM.png)/JST-SM-F |
| Lane 3 | [WS2812 PCB](WS2812_PCB.png) | 130mm/130mm tail | 26-30ga | [JST-SM-M](JST-XH_JST-SM.png)/JST-SM-F |
| Lane 4 | [WS2812 PCB](WS2812_PCB.png) | 130mm/130mm tail | 26-30ga | [JST-SM-M](JST-XH_JST-SM.png)/JST-SM-F |
| Jumper | |  80mm | 26-30ga | JST-XH-3/JST-SM-F |

##  N20 motors for Respoolers
| Lane | Component | Recommended Wire Length | Recommended Wire Gauge | Connector |
| ---- | --- | --- | ---| --- |
| Lane 1 | [N20 6V 500RPM](N20_6V_500RPM.png) | 205mm | 26ga | JST-XH-2 |
| Lane 2 | [N20 6V 500RPM](N20_6V_500RPM.png) | 315mm | 26ga | JST-XH-2 |
| Lane 3 | [N20 6V 500RPM](N20_6V_500RPM.png) | 415mm | 26ga | JST-XH-2 |
| Lane 4 | [N20 6V 500RPM](N20_6V_500RPM.png) | 515mm | 26ga | JST-XH-2 |

## Trigger (PREP) sensors
| Lane | Component | Recommended Wire Length | Recommended Wire Gauge | Connector |
| ---- | --- | --- | ---| --- |
| Lane 1 | [D2F-L w/ Lever](D2F_W-Lever.png) | 155mm | 26ga | JST-XH-3 |
| Lane 2 | [D2F-L w/ Lever](D2F_W-Lever.png) | 235mm | 26ga | JST-XH-3|
| Lane 3 | [D2F-L w/ Lever](D2F_W-Lever.png) | 335mm | 26ga | JST-XH-3 |
| Lane 4 | [D2F-L w/ Lever](D2F_W-Lever.png) | 435mm | 26ga | JST-XH-3 |

## Extruder (LOAD) sensors
| Lane | Component | Recommended Wire Length | Recommended Wire Gauge | Connector |
| ---- | --- | --- | ---| --- |
| Lane 1 | [D2HW-C201](D2HW-C201H.png) | 200mm | 26ga | JST-XH-3 |
| Lane 2 | [D2HW-C201](D2HW-C201H.png) | 310mm | 26ga | JST-XH-3 |
| Lane 3 | [D2HW-C201](D2HW-C201H.png) | 410mm | 26ga | JST-XH-3 |
| Lane 4 | [D2HW-C201](D2HW-C201H.png) | 465mm | 26ga | JST-XH-3 |

## Hub (HUB) sensor
| Component | Recommended Wire Length | Recommended Wire Gauge | Connector |
| --- | --- | ---| --- |
| [D2HW-C201](D2HW-C201H.png) | 510mm | 26ga | JST-XH-3 |

## TurtleNeck (TN) sensors
| Component | Recommended Wire Length | Recommended Wire Gauge | Connector | Notes |
| --- | --- | ---| --- | ---- |
| [D2F-L w/ Lever](TN_D2L_500_X2.png)  | 500mm | 26ga | JST-XH-3 | Quantity 2 |

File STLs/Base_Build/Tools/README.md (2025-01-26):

- PTFE_cutter.stl courtsey of Blamm
- motor_mount_helper.stl modeled by Tuxedo
- hub_tool_step1/step2.stl modeled by Johnjrk

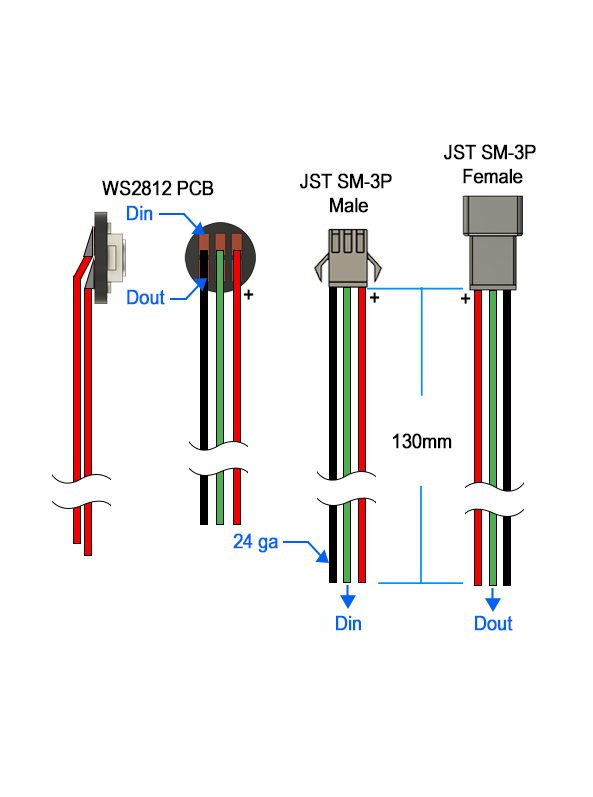
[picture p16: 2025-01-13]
BT_Wiring/WS2812_PCB.png

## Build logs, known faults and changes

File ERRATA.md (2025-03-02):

# BoxTurtle Errata

Below are issues that were not able to be corrected in time for v1.0 release.

## AFC-Lite v1.0 USB connector orientation
While BoxTurtle was originally designed for connecting with CAN bus (and that is still the recommended configuration if possible), it can also be connected with USB for data communications.

If you have an AFC-Lite v1.0 board, the USB connector faces outward in an orientation that is not optimal for a regular USB-C plug in the stock mounting position. This was corrected with AFC-Lite v1.1. As a workaround, use a right-angle USB-C cable or adapter to connect the BoxTurtle.

## LDO Kit known issues
### 30 Tooth MJF gear loose (Batch 1 & 2)
The 30 tooth MJF gears provided in the kit will likely be too loose to use as-is on the 8 x 80mm shaft. Either print the [FDM version of the gears](https://github.com/ArmoredTurtle/BoxTurtle/blob/main/STLs/Base_Build/Spooler/helical_gear_30_teeth_x4.stl) or secure the MJF gear with some glue at the appropriate position on the shaft (using the installation tool).  Make sure to not glue the gear to the installation jig! Also ensure that any glue residue is removed that would prevent the spacer from sitting flush against the gear.

### TurtleNeck switches missing levers (Batch 1)
The TurtleNeck switches are missing the required metal levers, and the FilamATrix switches have levers. Follow [this guide](https://www.youtube.com/watch?v=1cHecdyxhpw) on how to migrate the switches from the FilamATrix switches to the TurtleNeck buffer switches.

### TurtleNeck switch cable labels (Batch 1)
The TurtleNeck switch cables are labeled 1 and 2 in Batch 1 kits. For simplicity, use "1" for the Advance switch and "2" for the Trailing switch.

### Missing wheel heatset/screws (Batch 1, 2)
Changes were made to the wheel design late in the beta process after hardware kits had been created/bagged/labeled. As such, the extra hardware required for the wheels (heatsets and M3x6 screws) are in a separate 'Hardware for Wheel' bag included in your kit.

### 3mm ID PTFE tubing (Batch 1)
The 3mm ID PTFE tubing is a bit short of length from the BOM.  Make sure you cut the 80mm lengths between the motor mount and extruder body first. The feeder inlet tubes are specified to be 50mm in the manual, but can easily be shorter at 40-45mm.

### No cable included to connect BoxTurtle to the printer (Batch 1, 2)
As each printer connection is different, cable was not included in batch 1 kits to connect the BoxTurtle to your printer. A 2x2 pin Molex connector is included in the kits for you to create your own cable to connect the AFC lite for power and (optionally) canbus data.

### N20 motor failure
If you encounter any suspected failure issue with your N20 respooler motors, please contact your reseller. LDO is conducting analysis on any failures.

### M3 heatset count for FilamATrix (Batch 1, 2)
If you are doing a new build of Clockwork2 there will not be sufficient heatsets in the bag - the kits were designed with an upgrade to an existing CW2 extruder in mind. Additionally the kits may be a 1-2 heatsets short for all components even after accounting for spares in the FilamATrix bag, this will be corrected in a future batch.

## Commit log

2024-11-20 Added PTFE cutter
    [PTFE_cutter.stl]
2024-11-22 Add links to wiring lengths to README.md
2024-11-25 Rename for manual consistency
    [[c]_corner_diffuser_x4.stl]
2024-11-30 Update for new respooler files to match manual
    [[a]_bearing_spacer_x8.stl, [a]_wheel_drive_x8.stl, [a]_wheel_x8.stl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]
2024-12-02 Delete CAD directory
    Deprecated Beta final release
    [Box Turtle Assembled.f3z, Box Turtle Assembled.step, Box Turtle Simplified.step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]
2024-12-02 Delete STLs directory
    Old beta final files
    [15t_installation_tool.stl, 30t_installation_tool.stl, Frame.stl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]
2024-12-03 Updated trays Added Hubs Added PTFE_cutter
    [PTFE_cutter.stl, [a]_hub.stl, [a]_hub_D2F.stl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]
2024-12-03 Seam Detail Fix
    [mono_skirt_front.stl, skirt_front_hex_L.stl, skirt_front_hex_R.stl]
2024-12-05 Update README.md
    Add TN pins to wiring diagram
2024-12-05 Fix logo inlay Add Feed Trigger Retainer
    [[a]_feed_trigger_retainer_x4.stl, [a]_logo_inlay.stl]
2024-12-08 Update wiring diagram for TN ports
2024-12-14 Fix BOM links for N20 motors and add alternate link
2024-12-22 Per-material filament ramming configuration no longer required in OrcaSlicer 2.2.0+
2024-12-22 Minor reordering, add link to jontek2's a better print start macro
2025-01-06 Fixed Side panel clearance on 250 mount Adjusted overhang angle on wheel drive for easier printing
    [[a]_wheel_drive_x8.stl, turtle_leg_250_x4.stl]
2025-01-11 Update BOM to include JST-SM, remove duplicative xlsx version
    [BT_BOM.xlsx]
2025-01-13 Updated WS2812_PCB wiring diagram
2025-01-14 duplicate wiring guide for the purposes of not breaking link in the manual :D
2025-01-18 Include high level guidance on printed part options for LDO BoxTurtle Kits
2025-01-18 Reorient monolith front and rear skirts at exact 45 degree angle to fit on ~305mm build plates.
    [mono_skirt_front.stl, mono_skirt_hub.stl, mono_skirt_passthrough.stl]
2025-01-18 Adjusted ECAS cutout
    [[a]_slide.stl, frame.stl]
2025-01-25 Add motor mount helper installation tool
    [motor_mount_helper.step, motor_mount_helper.stl]
2025-01-26 add hub ecas installation helpers
    [hub_tool_step1.step, hub_tool_step1.stl, hub_tool_step2.step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]
2025-01-27 Update wiring guide
2025-01-31 Add turtleneck horizontal mount
    [turtleneck_horizontal_mount.stl]
2025-01-31 remove from this branch
    [turtleneck_horizontal_mount.stl]
2025-01-31 Add turtleneck_horizontal_mount.stl
    [turtleneck_horizontal_mount.stl]
2025-01-31 changed built-in supports
    [corner_printed_x4.stl]
2025-02-02 Update LDO convenience zip file with new mounts/tools, remove LED corner and p bottom panel spacers
2025-02-02 Add page about automatic stl configurator
2025-02-02 Update STL files
2025-02-02 Update wiring guide with note on chaining LED indicators
2025-02-02 Correct enclosure repo name
2025-02-02 Update turtleneck lid.stl
    [lid.stl]
2025-02-06 Added extra retention to hub switch
    [[a]_hub.stl]
2025-02-06 Updated CAD to latest
2025-02-06 Add note about N20 motor mounts and first layers
2025-02-06 add note about power requirements for 24V
2025-02-06 sync stl zip from main
2025-02-09 Delete STLs/Option_Parts/depressor_x4.stl
    placeholder
    [depressor_x4.stl]
2025-02-09 Update ERRATA.md with note about FilamATrix heatsets
2025-02-15 Added BT voron hard mount CAD
    [BT_Voron_hard_mount.step]
2025-02-15 Add SteveBuild's skirts to the Option_Parts folder
    [Hex_Front_1pc.f3d, Hex_Front_1pc_Mesh.stl, Hex_Front_1pc_Solid.step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]
2025-02-15 Remove LFS bits
    [Hex_Side_1pc_Solid.step, hub_tool_step1.step, hub_tool_step2.step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]
2025-02-17 Loaded LED is green, not white.
2025-02-21 Add pre-cut STLs of modeled mesh skirts
    [Hex_Front_Part1_Mesh.stl, Hex_Front_Part2_Mesh.stl, Hex_Rear_Center_Hub_Mesh.stl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]
2025-02-21 Add TN switch issue to Errata
2025-03-14 Make note on printed parts recommendations more prominent
